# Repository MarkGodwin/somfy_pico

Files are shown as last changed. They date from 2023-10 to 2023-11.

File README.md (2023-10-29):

# Pico Somfy - What is that?

I found a way to get the RFM69HCW "packet mode" to produce packets that were compatible with the Somfy RTS protocol
This is the result of that experiment getting way out of hand:

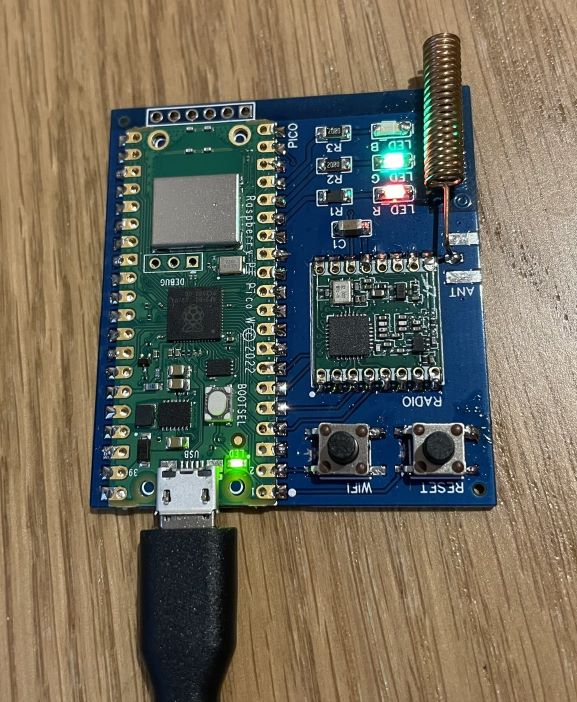
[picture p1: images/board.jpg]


Pico Somfy in a DIY hardware project for controlling Somfy Blinds in Home Assistant (or with MQTT/HTTP). It also listens to
signals from real Somfy remotes, so it can know if the blinds have been moved outside of its control. This is useful because
the Somfy protocol is one-way.

 It can be put together using a cheap Raspberry PI Pico W and an RFM69HCW module. You can put this together on a breadboard, but it's very very cheap to manufacture a prototype PCB now too.

The (my first) EasyEDA PCB layout is provided in the pcb folder. You can get 5 boards manufactured by JLC PCB about $5, delivered!

The Pi Pico W runs a small React web interface that lets you configure blinds and any additional remotes.
Blinds are exposed to Home Assistant through MQTT discovery as Covers. The position of the blinds are estimated
based on open/close timings.

Additional Remotes can be created, and bound to several blinds, to allow group control.
These are exposed to home assistant as buttons, not covers. Operating a remote will update the position of the associated covers.

With JLC PCB, total cost to manufacture the PCB and buy the parts is about £20.

## Parts

Required:
* [Pi Pico W](https://www.mouser.co.uk/ProductDetail/358-SC0918) - £4.80
* [RFM69HCW 433Mhz](https://www.mouser.co.uk/ProductDetail/474-COM-13910) - £4.99
* [Ceramic Capacitor](https://www.mouser.co.uk/ProductDetail/187-CL31A106KAHNNNE) - £0.06 (or you can buy the Adafruit breadboard module which includes the capacitor on-board)

Optional:
* Status LEDs
  * [Red](https://www.mouser.co.uk/ProductDetail/645-599-0220-007F) - £0.18 + [Resistor](https://www.mouser.co.uk/ProductDetail/71-CRCW1206220RFKEB) - £0.03
  * [Green](https://www.mouser.co.uk/ProductDetail/645-599-0281-007F) - £0.28 + [Resistor](https://www.mouser.co.uk/ProductDetail/71-CRCW120620R0FKEAC) - £0.03
  * [Blue](https://www.mouser.co.uk/ProductDetail/645-599-0291-007F) - £0.21 + [Resistor](https://www.mouser.co.uk/ProductDetail/71-CRCW120620R0FKEAC) - £0.03
* Tactile Switches x 2 - I bought ones with the wrong pins cross-connected. Oh well.
* There is a position for an edge-mount antenna connector. I couldn't find a cheap option to use, but a better
  antenna really isn't needed anyway. Any short bit of wire would probably do.

## Building the Firmware

* Open Visual Studio Code in the `firmware` folder. 
* From the terminal run `./generate_fsdata.sh`. This builds the web interface project, which is then squeezed onto the Pi Pico.
* Use the CMake plugin to build the project using the unspecified architecture. This will automatically use the Pico SDK.

## Installing the Firmware

Hold down BootSel while plugging in the Pi Pico W.
Copy the `somfy_remote.uf2` file from the `build/` directory to the Pico drive that appears.
If you need to update the firmware, you can re-enter firmware mode via the web interface too.

## Getting Started

When initially started for the first time, the pico starts in WiFi setup mode (green status LED shows).
It will appear as a WiFi access point called "pico_somfy". Connect to that access point with the password "password".

Go to http://192.168.4.1 to access the setup interface. Here you can select your Wifi network from the drop-down list
and enter your WiFi credentials so Pico Somfy can connect to your network. Note: Pi Pico only supports Wifi 2.4G.

Click Save & Reboot.

Pico Somfy should start up and connect to the Wifi network. You should see a pulsing red light which indicates WiFi
is connected and has an IP address assigned.
If the light does not light, the WiFi connection could not be established. You can re-enter WiFi setup mode by pressing
Reset for a short press, and then holding the WiFi button for about 10 seconds during startup until the green LED
lights steadily.

Next, Figure out what IP address your Pico Somfy has been assigned. You can get this from your router. The device should
show up as pico_somfy in your router client list. Then go to the web interface at http://&lt;your-pico-ip-here&gt;
to configure your Pico Somfy.

You can then go to the Network Setup page to add your MQTT configuration settings. This is required for Home Assistant integration.
Once MQTT is connected, you will see a pulsing green status light.

Blinds can be added from the Control Blinds page. I reccomend you add a blind for each blind you want to control first
and then add additional remotes to group them together as required.

If you want to import a real remote, there is a button for that. This allows you to bind the real
remote to your blind instances, so that the system knows which blinds will move when the remote is
activated. While you can issue commands as if they came from the real remote, this will get the
rolling codes out-of-sequence, so isn't a good idea. Better to create a new blind remote, and use
the Somfy copy/paste.

You can bind remotes to blinds in the edit page:

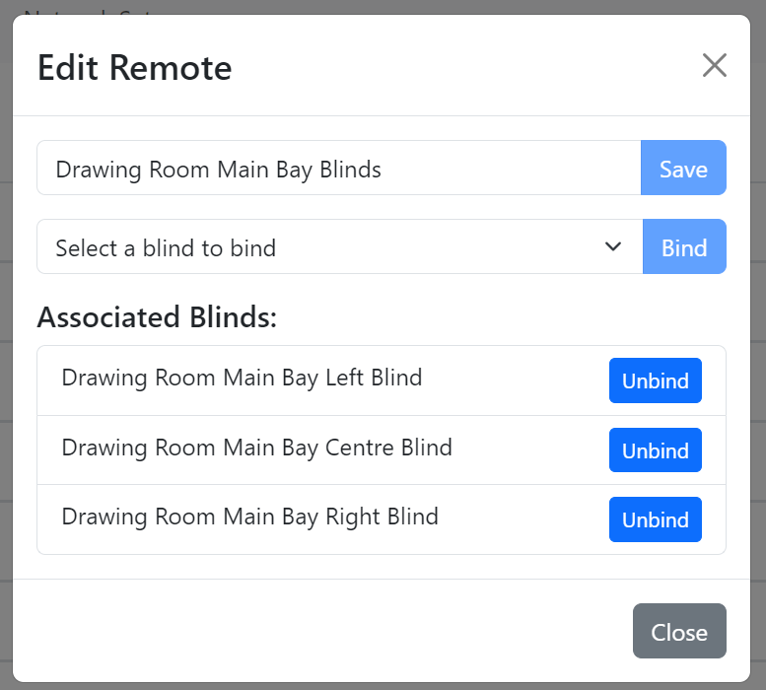
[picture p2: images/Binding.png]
;

The Blind control page and interface is pretty rough around the edges, and not designed to be used for any
more than setting up the blinds and testing the functions. Use Home Assistant or the MQTT/HTTP API for control
and automation.

## Somfy Commands - For reference

To add a remote to a brand new blind (or after a factory reset), long press the up-down buttons.
This then enters the blind setup procedure where you can use various button combinations to set
the direction of the blinds and the blind limits.

To configure a blind that already has a remote associated with it, long-press the program button
on the existing remote. Then short-press the program button on the new blind's remote (see the ...
button on the blind controls):

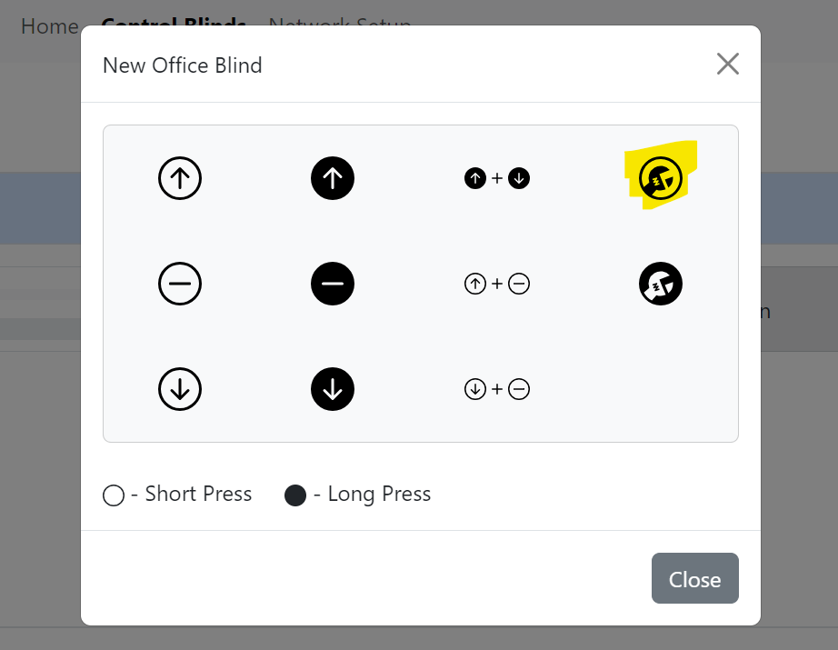
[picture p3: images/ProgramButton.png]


Some Somfy documentation says you need a long-press. This may be true of some blinds, but not mine.

Adding additional remotes has a built-in bind/unbind feature in the web interface. Choose which
of your existing blinds you want the remote to control.

## Enclosure

I designed a simple 6cm x 6cm x 1.5cm square case to hold the circuit board and expose the buttons and status LEDs.

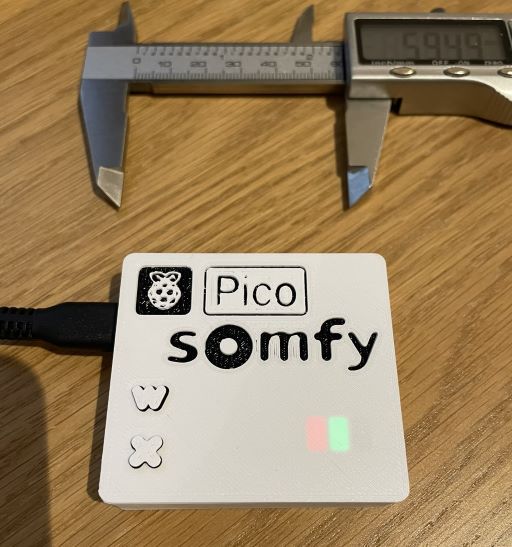
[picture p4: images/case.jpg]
Case
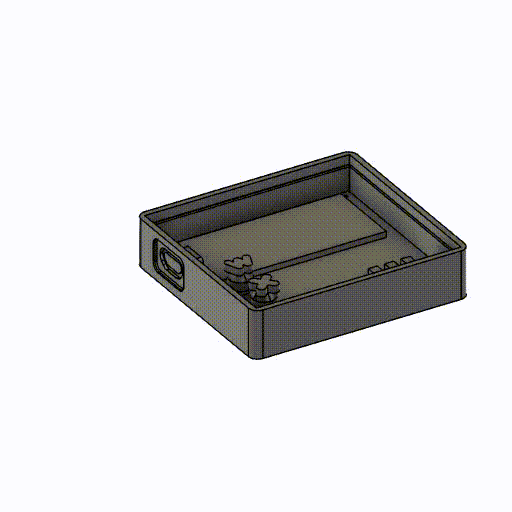
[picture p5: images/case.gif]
Animation


The Fusion 360 and STL files ca be found in the `case/` directory. Print the lid and buttons face-down.
No Supports are needed. I changed filament half way through printing the lid to make the recessed logo
stand out.

## Future

- I've found some sources detailing other Somfy remote code standards which should be fairly easy to add. I don't have these blinds so I can't test this
- At the moment, we don't have any good way of activating tilt on a tilt & lift blind. I think there are various chords of button presses needed to activate these, depending on the blind & region
- The web UI do with some serious polish

## Credits

This project relied heavily on the Somfy RTS protocol decoding which was done by [PushStack](https://pushstack.wordpress.com/somfy-rts-protocol/).

The original idea came from the Pi-Somfy project from [Nickduino](https://github.com/Nickduino/Pi-Somfy). This fantastic project is only let down by the unreliable radio module whose radio frequency would seemingly change with the weather.
I started trying out the RFM69 module instead, but ended up trying to control it from a £6 Pico W for what was
supposed to be "fun".

## License

MIT Open Source license.

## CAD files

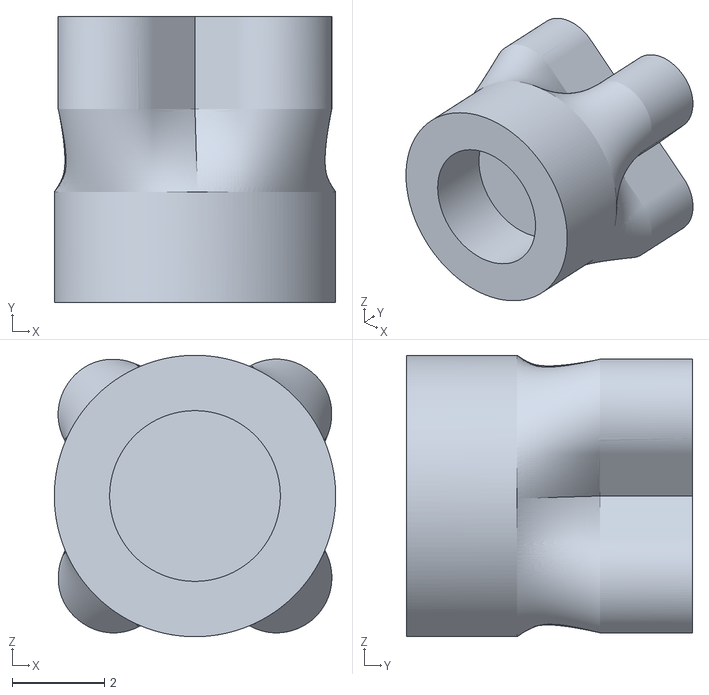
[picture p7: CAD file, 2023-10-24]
case/PicoSomfyResetButton.stl
6.10 x 6.20 x 6.10

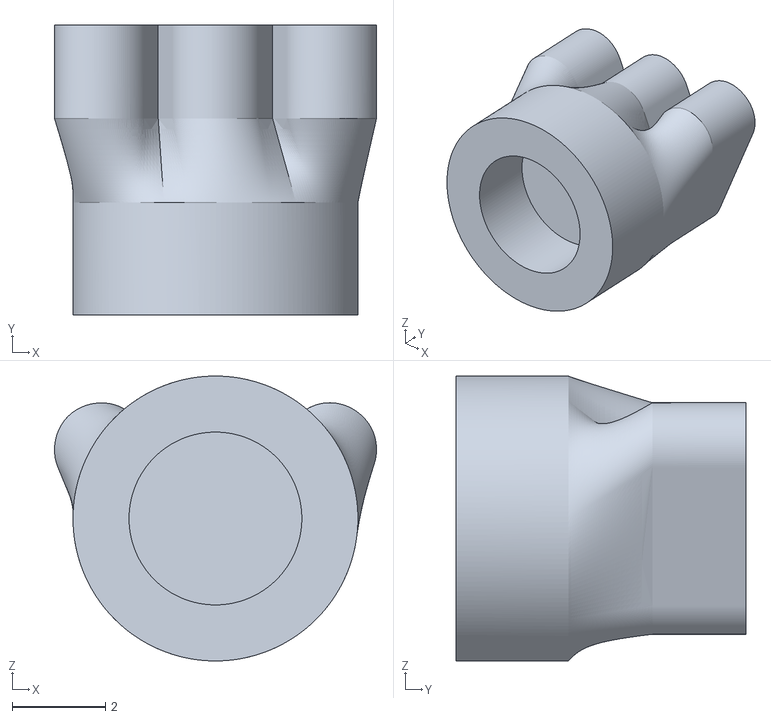
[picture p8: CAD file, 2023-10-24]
case/PicoSomfyWifiButton.stl
6.89 x 6.20 x 6.10

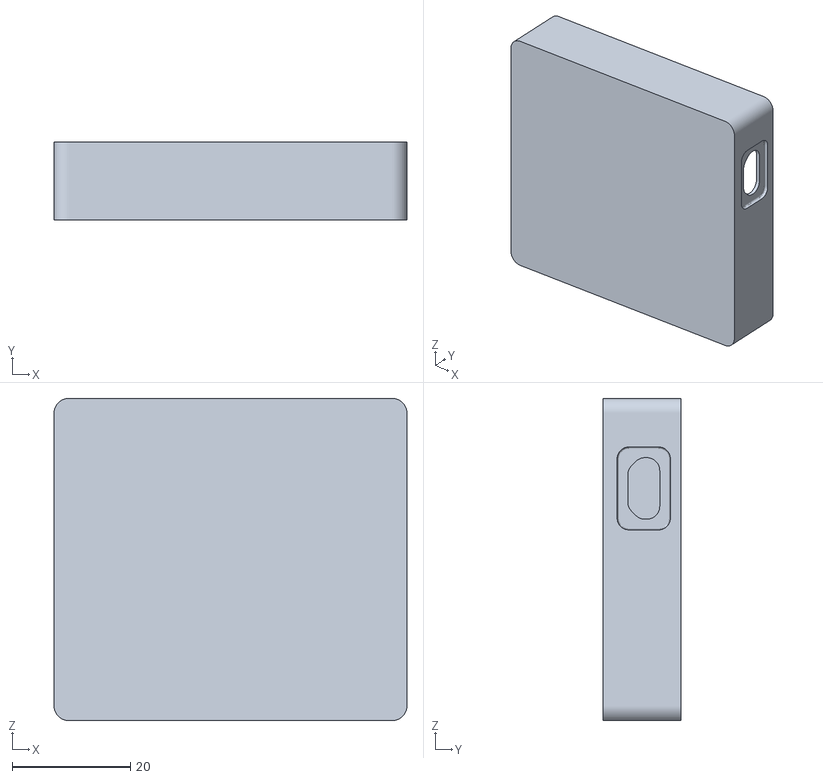
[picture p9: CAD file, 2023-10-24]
case/PicoSomfyBase.stl
59.6 x 13.2 x 54.4

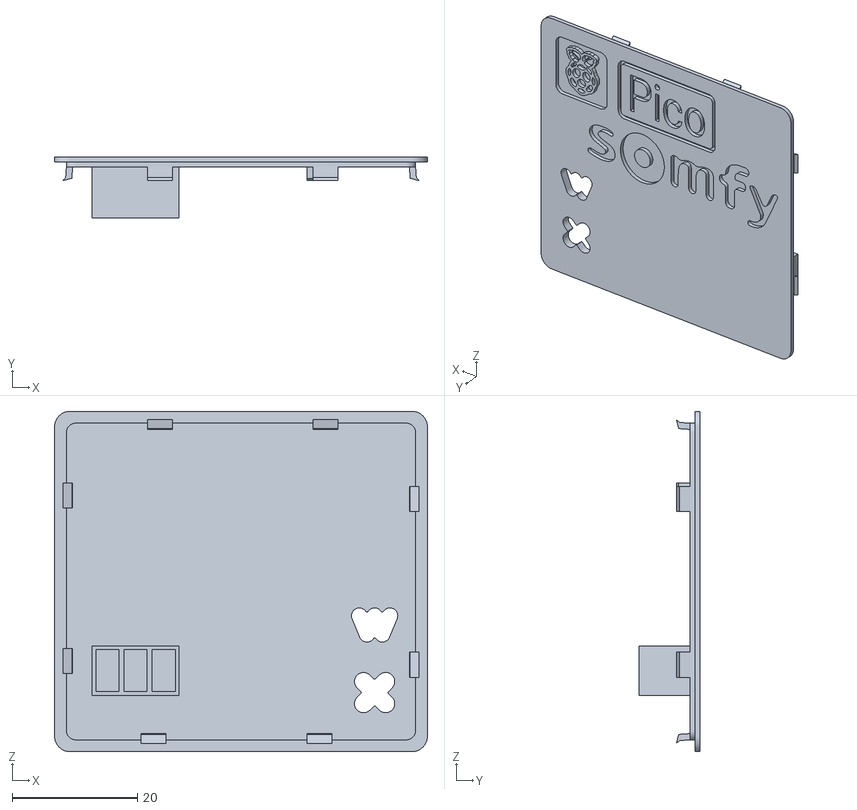
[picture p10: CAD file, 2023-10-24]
case/PicoSomfyLid3.stl
59.6 x 9.80 x 54.4

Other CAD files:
case/PicoSomfy Case v11.f3d

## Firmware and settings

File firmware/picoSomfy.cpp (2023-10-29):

// Copyright (c) 2023 Mark Godwin.
// SPDX-License-Identifier: MIT
//
// Main entry point!

#include "picoSomfy.h"
#include "hardware/spi.h"
#include "hardware/pio.h"
#include "hardware/watchdog.h"
#include "pico/cyw43_arch.h"
#include "pico/flash.h"
#include "pico/bootrom.h"
#include "lwip/pbuf.h"
#include "lwip/tcp.h"

#include "radio.h"
#include "remotes.h"
#include "blinds.h"
#include "wifiConnection.h"
#include "wifiScanner.h"
#include "webServer.h"
#include "mqttClient.h"
#include "blockStorage.h"
#include "configService.h"
#include "deviceConfig.h"
#include "serviceStatus.h"
#include "serviceControl.h"
#include "statusLed.h"
#include "commandQueue.h"

// SPI Defines
// We are going to use SPI 0, and allocate it to the following GPIO pins
// Pins can be changed to some extent, see the GPIO function select table in the datasheet for information on GPIO assignments
#define SPI_PORT spi_default
#define PIN_MISO 4
#define PIN_SCK  2
#define PIN_MOSI 3
#define PIN_CS_RADIO   5

// Hard buttons
#define PIN_RESET 0
#define PIN_WIFI 1

// Status LED
#define PIN_LED_R 11
#define PIN_LED_G 12
#define PIN_LED_B 13

// How much flash memory to use to store blind/remote/wifi config. Beware changing these as it will corrupt the block storage
#define STORAGE_SECTORS 32
#define STORAGE_BLOCK_SIZE 252

// Radio hardware reset
#define PIN_RESET_RADIO 15
// Radio IRQ on packet status
#define PIN_RADIO_PACKET 14

const WifiConfig *checkConfig(
    std::shared_ptr<DeviceConfig> config,
    StatusLed *statusLed);

void runServiceMode(
    std::shared_ptr<WebServer> webServer,
    std::shared_ptr<DeviceConfig> config,
    std::shared_ptr<WifiConnection> wifiConnection,
    std::shared_ptr<RadioCommandQueue> commandQueue,
    std::shared_ptr<ServiceControl> service,
    StatusLed *mqttLed);

void runSetupMode(
    std::shared_ptr<WebServer> webServer,
    std::shared_ptr<ServiceControl> service);

bool checkButtonHeld(int inputPin, StatusLed *led);

void doPollingSleep(uint ms)
{
#if PICO_CYW43_ARCH_POLL
    auto wakeTime = make_timeout_time_ms(ms);
    //auto totalPollTime = 0ll;
    //auto totalWaitTime = 0ll;
    do
    {
        //auto startPoll = get_absolute_time();
        cyw43_arch_poll();
        //auto endPoll = get_absolute_time();
        //totalPollTime += absolute_time_diff_us(startPoll, endPoll);
        cyw43_arch_wait_for_work_until(wakeTime);
        //totalWaitTime += absolute_time_diff_us(endPoll, get_absolute_time());
    } while(absolute_time_diff_us(get_absolute_time(), wakeTime) > 0);

    //if(totalPollTime > totalWaitTime)
    //{
    //    DBG_PRINT("Long poll: %u/%u ms\n", (int)(totalPollTime/1000), ms);
    //}
    
#else
    // We're using background IRQ callbacks from LWIP, so we can just sleep peacfully...
    sleep_ms(ms);
#endif
}

int main()
{
#ifndef NDEBUG
    stdio_init_all();
#endif

    // Set up pins for the hard buttons
    gpio_init(PIN_RESET);
    gpio_set_dir(PIN_RESET, GPIO_IN);
    gpio_set_pulls(PIN_RESET, true, false);
    gpio_init(PIN_WIFI);
    gpio_set_dir(PIN_WIFI, GPIO_IN);
    gpio_set_pulls(PIN_WIFI, true, false);

    gpio_init(PIN_RADIO_PACKET);
    gpio_set_dir(PIN_RADIO_PACKET, GPIO_IN);

    // SPI initialisation. Set SPI speed to 0.5MHz. Absolute max supported is 10Mhz
    spi_init(SPI_PORT, 500*1000);
    gpio_set_function(PIN_MISO, GPIO_FUNC_SPI);
    gpio_set_function(PIN_SCK,  GPIO_FUNC_SPI);
    gpio_set_function(PIN_MOSI, GPIO_FUNC_SPI);

    // LED timers need the async context set up to work
    if (cyw43_arch_init()) {
        sleep_ms(6000);
        DBG_PUT("Pico init failed");
        return -1;
    }

    StatusLed redLed(PIN_LED_R);
    StatusLed greenLed(PIN_LED_G);
    StatusLed blueLed(PIN_LED_B);

    // Pointless startup cycle, to give me enough time to start putty
    redLed.Pulse(256, 768, 128);
    doPollingSleep(2000);
    greenLed.Pulse(128, 512, 128);
    doPollingSleep(2000);
    blueLed.Pulse(128, 512, 128);
    doPollingSleep(2000);

    redLed.TurnOff();
    greenLed.TurnOff();
    blueLed.TurnOff();

    DBG_PUT("Starting the Radio");
    auto radio = std::make_shared<RFM69Radio>(SPI_PORT, PIN_CS_RADIO, PIN_RESET_RADIO, PIN_RADIO_PACKET);

    // We'll run radio commands from the core 1 thread
    auto commandQueue = std::make_shared<RadioCommandQueue>(radio, &blueLed);
    DBG_PUT("Starting worker thread...");
    commandQueue->Start();

    // Store flash settings at the very top of Flash memory
    // ALL STORED DATA WILL BE LOST IF THESE ARE CHANGED
    const uint32_t StorageSize = STORAGE_SECTORS * FLASH_SECTOR_SIZE;

    auto config = std::make_shared<DeviceConfig>(StorageSize, STORAGE_BLOCK_SIZE);
    auto wifiConfig = checkConfig(config, &redLed);
    if(wifiConfig == nullptr)
    {
        redLed.SetLevel(1024);
        blueLed.SetLevel(1024);
        return -1;
    }

    auto apMode = !wifiConfig->ssid[0];

    auto service = std::make_shared<ServiceControl>();

    if(checkButtonHeld(PIN_WIFI, &greenLed))
    {
        DBG_PUT("Starting in WIFI Setup mode, as button WIFI button is pressed");
        apMode = true;
    }

    DBG_PUT("Starting the WiFi Scanner...");
    auto wifiLed = apMode?&greenLed:&redLed;
    auto wifiConnection = std::make_shared<WifiConnection>(config, apMode, wifiLed);

    // Do an initial WiFi scan before entering AP mode. We don't seem to be able
    // to scan once in AP mode.
    auto wifiScanner = std::make_shared<WifiScanner>(apMode);
    wifiScanner->WaitForScan();

    // Now connect to WiFi or Enable AP mode
    DBG_PRINT("Enabling WiFi in %s mode...\n", apMode ? "AP" : "Client");
    wifiConnection->Start();

    DBG_PUT("Starting the web interface...");
    auto webServer = std::make_shared<WebServer>(config, wifiConnection, wifiLed);
    webServer->Start();
    auto configService = std::make_shared<ConfigService>(config, webServer, wifiScanner, service);

    if(apMode)
    {
        runSetupMode(webServer, service);
    }
    else
    {
        runServiceMode(webServer, config, wifiConnection, commandQueue, service, &greenLed);
    }

    DBG_PUT("Restarting now!");
    doPollingSleep(1000);

    if(service->IsFirmwareUpdateRequested())
    {
        reset_usb_boot(0,0);
    }
    else
    {
        watchdog_reboot(0,0,500);
    }
    doPollingSleep(5000);
    DBG_PUT("ERM!!! Why no reboot?");

}

bool checkButtonHeld(int inputPin, StatusLed *led)
{
    int a = 0;
    for(a = 0; !gpio_get(inputPin) && a < 100; a++)
    {
        if(a == 0)
            led->Pulse(1024, 2048, 256);
        doPollingSleep(50);
    }
    led->TurnOff();
    return a == 100;
}

const WifiConfig *checkConfig(
    std::shared_ptr<DeviceConfig> config,
    StatusLed *redLed)
{
    DBG_PUT("Checking Device config...");
    
    auto needReset = config->GetWifiConfig() == nullptr;
    if(needReset)
        DBG_PUT("WiFi Config not found.");
    else
    {
        needReset = checkButtonHeld(PIN_RESET, redLed);
    }

    if(needReset)
    {
        DBG_PUT("Resetting all settings!");
        config->HardReset();
    }

    auto wifiConfig = config->GetWifiConfig();
    if(wifiConfig == nullptr ||
        config->GetMqttConfig() == nullptr)
    {
        DBG_PUT("Settings could not be read back. Error!\n");
        return nullptr;
    }
    return wifiConfig;
}

void runServiceMode(
    std::shared_ptr<WebServer> webServer,
    std::shared_ptr<DeviceConfig> config,
    std::shared_ptr<WifiConnection> wifiConnection,
    std::shared_ptr<RadioCommandQueue> commandQueue,
    std::shared_ptr<ServiceControl> service,
    StatusLed *mqttLed)
{

    auto mqttClient = std::make_shared<MqttClient>(config, wifiConnection, "pico_somfy/status", "online", "offline", mqttLed);

    mqttClient->Start();
    // Subscribe by wildcard to reduce overhead
    mqttClient->SubscribeTopic("pico_somfy/blinds/+/cmd");
    mqttClient->SubscribeTopic("pico_somfy/blinds/+/pos");
    mqttClient->SubscribeTopic("pico_somfy/remotes/+/cmd");

    auto blinds = std::make_shared<Blinds>(config, mqttClient, webServer);
    auto remotes = std::make_shared<SomfyRemotes>(config, blinds, webServer, commandQueue, mqttClient);
    blinds->Initialize(remotes);

    ServiceStatus statusApi(webServer, mqttClient, false);

    ScheduledTimer republishTimer([&blinds, &remotes] () {
        // Try to republish discovery information for one device
        // It should be safe to access the collections from this callback.
        if(remotes->TryRepublish()||
            blinds->TryRepublish())
            // Do another later, if there is more work to be done
            // We can't publish everything at once, as lwip needs a chance to run to clear the queues
            return 100;

        // Everything that needed to be published has been
        return 0;
    }, 0);

    auto mqttConnected = false;

    auto asyncContext = cyw43_arch_async_context();

    DBG_PUT("Entering main loop...");
    bool resetPushed = false;
    while(!service->IsStopRequested()) {

        doPollingSleep(250);

        // Lazy man's notification of MQTT reconnection outside of an IRQ callback
        if(!mqttConnected)
        {
            if(mqttClient->IsConnected())
            {
                mqttConnected = true;
                republishTimer.ResetTimer(250);
            }
        }
        else if(!mqttClient->IsConnected())
        {
            republishTimer.ResetTimer(0);
            mqttConnected = false;
        }

        // Check for recieved Somfy messages
        SomfyCommand cmd;
        if(commandQueue->ReadCommand(&cmd))
        {
            // A button on someone else's remote has been pressed. If it's a remote we care about
            // update the state of any blinds attached to that remote
            remotes->ExternalButtonPress(cmd);
        }

        if(!gpio_get(PIN_RESET))
        {
            if(resetPushed)
            {
                DBG_PUT("Reset pushed!");
                service->StopService(false);
            }
            resetPushed = true;
        }
        else
        {
            resetPushed = false;
        }
        if(!gpio_get(PIN_WIFI))
        {
            // TODO: Reset WiFi or something in this case?
            DBG_PUT("WIFI pushed");
        }

    }

    republishTimer.ResetTimer(0);

    DBG_PUT("Waiting for the command queue to clear...");
    commandQueue->Shutdown();


    DBG_PUT("Saving any unsaved state.\n");
    remotes->SaveRemoteState();
    blinds->SaveBlindState(true);

}

void runSetupMode(
    std::shared_ptr<WebServer> webServer,
    std::shared_ptr<ServiceControl> service)
{
    ServiceStatus statusApi(webServer, nullptr, true);

    DBG_PUT("Entering setup loop...");
    auto onOff = false;
    while(!service->IsStopRequested()) {

        doPollingSleep(1000);

        if(!gpio_get(PIN_RESET))
        {
            DBG_PUT("Reset pushed");
            service->StopService();
        }
        if(!gpio_get(PIN_WIFI))
            DBG_PUT("WIFI pushed");
    }

}

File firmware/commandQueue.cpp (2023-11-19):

// Copyright (c) 2023 Mark Godwin.
// SPDX-License-Identifier: MIT
// TODO: Make this a generic command queue

#include "picoSomfy.h"
#include "pico/multicore.h"
#include "pico/flash.h"
#include <string.h>
#include "commandQueue.h"
#include "radio.h"
#include "statusLed.h"
#include "remote.h"

struct CommandEntry
{
    uint32_t commandType;
    uint32_t remoteId;
    uint16_t rollingCode;
    uint16_t repeat;
    SomfyButton button;
};

class SpinLock
{
public:
    SpinLock(spin_lock_t *lock): _lock(lock)
    {
        _irq = spin_lock_blocking(_lock);
    }
    ~SpinLock()
    {
        spin_unlock(_lock, _irq);
    }

private:
    spin_lock_t *_lock;
    int32_t _irq;
};

RadioCommandQueue::RadioCommandQueue(std::shared_ptr<RFM69Radio> radio, StatusLed *led)
:   _radio(std::move(radio)),
    _led(led),
    _recvWrite(0),
    _recvRead(0),
    _recvCount(0)
{
    queue_init(&_queue, sizeof(CommandEntry), 16);
    _lockNum = spin_lock_claim_unused(true);
    _recvLock = spin_lock_init(_lockNum);
}

bool RadioCommandQueue::QueueCommand(SomfyCommand command)
{
    CommandEntry entry = { 
        commandType: 1,
        remoteId: command.remoteId,
        rollingCode: command.rollingCode,
        repeat: command.repeat,
        button: command.button
    };

    return queue_try_add(&_queue, &entry);
}

bool RadioCommandQueue::ReadCommand(SomfyCommand *command)
{
    auto now = get_absolute_time();

    // CRITICAL SECTION
    SpinLock scopedLock(_recvLock);

    if(!_recvCount)
        // Nothing is waiting to be picked up
        return false;

    if(absolute_time_diff_us(_receivedCommands[_recvRead].lastMsgTime, now) < 250000)
        // More of the command repeates might be incoming
        return false;

    command->remoteId = _receivedCommands[_recvRead].command.remoteId;
    command->rollingCode = _receivedCommands[_recvRead].command.rollingCode;
    command->repeat = _receivedCommands[_recvRead].command.repeat;
    command->button = _receivedCommands[_recvRead].command.button;
    _recvCount--;
    _recvRead = (_recvRead + 1) % (MAX_RECV_QUEUE);
    if(_recvCount == 0)
        _recvWrite = _recvRead;
    return true;
}

void RadioCommandQueue::Shutdown()
{
    CommandEntry entry = { 
        commandType: 0
    };

    queue_add_blocking(&_queue, &entry);

    // Wait until our Stop command is removed from the queue
    while(queue_get_level(&_queue))
    {
        sleep_ms(100);
    } 
}

/// @brief Called when there is a packet to be read from the radio
void RadioCommandQueue::QueueReceive()
{
    CommandEntry entry = { 
        commandType: 2
    };

    queue_try_add(&_queue, &entry);
}

// HACK. But there can be only 1 anyway
static RadioCommandQueue *_thequeue = nullptr;

void RadioCommandQueue::Start()
{

    _thequeue = this;
    multicore_launch_core1([]() {
        // Make sure the other core can fiddle with flash without us screwing everything up
        if(!flash_safe_execute_core_init())
        {
            // Unsafe to continue this thread...
            DBG_PUT("Flash init failed");
            return;
        }

        _thequeue->Worker();

        // Don't actually end the command thread, as we want to write to flash
        // and if we stop this thread, the flash write may fail because it can't
        // synchronise
        while(true)
            sleep_ms(1000);

        //flash_safe_execute_core_deinit();
    });
}

void RadioCommandQueue::Worker()
{
    _led->SetLevel(512);
    _radio->Reset();
    DBG_PUT("Radio Reset complete!");
    _radio->Initialize();
    _radio->SetSymbolWidth(640);
    _radio->SetFrequency(433.42);
    auto fq = _radio->GetFrequency();
    DBG_PRINT("Radio frequency: %.3f\n", fq);
    auto br = _radio->GetBitRate();
    DBG_PRINT("BitRate: %dbps\n", br);
    auto ver = _radio->GetVersion();
    DBG_PRINT("Radio version: 0x%02x\n", ver);
    _led->SetLevel(0);

    while(true)
    {
        
        // Don't enter RX mode if there is already another packet waiting to be sent
        if(queue_is_empty(&_queue))
        {
            // Enter RX mode while we wait...
            // Wait for the end of any sync bytes (both initial and repeat ends the same way)
            // By offsetting the sync bytes by 1 bit, we get good reception... The sync pulses
            // from the genuine remotes don't match the main signal section symbol width exactly.
            uint8_t syncBytes[] = {0xE1, 0xE1, 0xFE};
            _radio->SetSyncBytes(syncBytes, sizeof(syncBytes));
            _radio->SetPacketFormat(true, 7);
            _radio->EnableReceive([]() { _thequeue->QueueReceive(); } );
        }

        CommandEntry entry;
        queue_remove_blocking(&_queue, &entry);
        _radio->Standby();

        switch(entry.commandType)
        {
            case 0:
                return;
            case 1:
                ExecuteCommand(entry.remoteId, entry.rollingCode, entry.button, entry.repeat);
                break;
            case 2:
                ReceiveCommand();
        }
    }
}

void RadioCommandQueue::ExecuteCommand(uint32_t remoteId, uint16_t rollingCode, SomfyButton button, uint16_t repeat)
{
    _led->SetLevel(1024);

    _radio->SetSyncBytes(NULL, 0);
    _radio->SetPacketFormat(false, 2);
    auto now = get_absolute_time();

    // Fog horn to wake up the blinds
    uint8_t fog[2];
    ::memset(fog, 0xFF, 2);
    _radio->TransmitPacket(fog, 16);
    _led->SetLevel(128);

    uint8_t payload[16] = {
        0x50,                       // "Key". Fixed...
        (uint8_t)(button << 4),
        (uint8_t)(rollingCode >> 8),
        (uint8_t)(rollingCode & 0xFF),
        (uint8_t)((remoteId >> 16) & 0xFF),
        (uint8_t)((remoteId >> 8) & 0xFF),
        (uint8_t)(remoteId & 0xFF),
    };
    memset(payload + 7, 0, 9);

    // Add the checksum
    uint8_t checksum = 0;
    for(auto a = 0; a < 7; a++)
        checksum ^= payload[a] ^ (payload[a] >> 4);
    payload[1] |= (checksum & 0x0F);

    // "Encrypt"
    for(auto a = 1; a < 7; a++)
        payload[a] ^= payload[a-1];

    const uint8_t syncBytes[] = { 0xF0, 0xF0, 0xF0, 0xF0, 0xF0, 0xF0, 0xF0, 0xFE };

    _radio->SetSyncBytes(syncBytes + 5, 3);
    _radio->SetPacketFormat(true, 7);
    auto packetStartTime = delayed_by_us(now, 29000); 
    while(absolute_time_diff_us(get_absolute_time(), packetStartTime) > 0);

    _led->SetLevel(1024);
    _radio->TransmitPacket(payload, sizeof(payload));
    _radio->SetSyncBytes(syncBytes, 8);
    packetStartTime = delayed_by_us(packetStartTime, 115000);
    _led->SetLevel(256);

    for(auto a = 0; a < repeat; a++)
    {
        while(absolute_time_diff_us(get_absolute_time(), packetStartTime) > 0);

        _led->SetLevel(1024);
        _radio->TransmitPacket(payload, sizeof(payload));
        _led->SetLevel(256);
        packetStartTime = delayed_by_us(packetStartTime, 139000);
    }
    _led->SetLevel(0);
}
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

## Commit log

2023-10-21 circuit board v1
2023-10-21 Rearrange layout. Add PCB
2023-10-22 Basic status leds. Gave up on PIO
2023-10-24 Case files
    [PicoSomfy Case v11.f3d, PicoSomfyBase.stl, PicoSomfyLid3.stl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]
2023-10-24 Better status LEDs. Add copyright. Polish
2023-10-24 Don't stop the command thread on shutdown
2023-10-26 Switch to polling to avoid strange progressive slowdown
    [somfy_remote.cpp, statusLed.cpp]
2023-10-29 Fix indent of DBG_ macros
    [commandQueue.cpp]
2023-11-19 Fixing sending commands in quick succession Always save current blind position Store My position on long press
    [commandQueue.cpp, radio.cpp]
